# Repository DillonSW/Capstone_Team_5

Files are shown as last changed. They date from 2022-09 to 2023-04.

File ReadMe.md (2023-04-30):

# Class Kit Vending Machine 

## Executive Summary

Every year hundreds of students require various devices for their ECE (Electrical and Computer Engineering) classes. These specific devices are provided by the College of Engineering and are rented out to students through the ECE office. Typically, in the first month of a semester, students attempt to check out on average 50 devices in a day from the Office. This capstone project will focus on designing and implementing a vending machine that can distribute devices out to students while recording which students have checked out a device. The finished product will be a vending machine with the functionality to vend the needed specific devices to students. A student can enter their information into the machine, and the machine will record who has checked out their respective device(s). The machine will use a motor to rotate a device to the door for a student to remove that has LEDs (Light Emitting Diode) which will allow students to see and determine which device is the one they should remove. The student will then take the device and shut the door for the next student.     

## Capabilities

The first prototype of the vending machine has the capability to record all input student data and store to the SQL database held on the host machine. The program can communicate using custom OPC software and read/write tags to turn the motor. The GUI has a loading mode where the admin can enter all devices inside the machine and a delete mode where all data held by the database can be removed. After loading, the machine resets to the initial position to track exactly which board will be rented. The motor is powered through the custom enclosure and is controlled by the PLC. The overall function of the machine allows a student to enter data and quickly receive a response from the machine, returning a board to the student and recording exactly which device was given.  

## Salient Outcomes

The team believes one salient outcome of this project is the development of a base communication program between a host machine and PLC. This project can serve as a platform for future teams to be able to create a full version of the kit vending machine for the ECE department. The communication is specifically between a linux machine and Allen Bradley PLC.  

The team also believes another outcome of the project is the protection of data through research into SQL Injection. This can also serve to teach future teams about data safety when using databases. SQL Injection is an issue many large companies deal with on a daily basis.  

## Project Demonstration & Images

Experimentation Videos:
* GUI system: https://youtu.be/tVvsogPO3sM  
* Safety System: https://youtu.be/iVfy9IWk9oA  
* PLC System: https://youtu.be/Vv9zIDt42ac  

**GUI Image**  

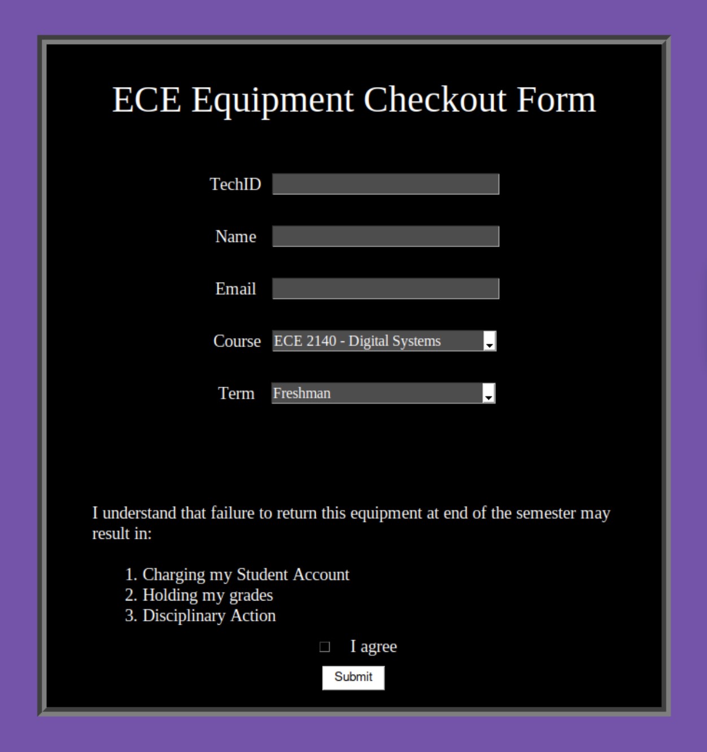
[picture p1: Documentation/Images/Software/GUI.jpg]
GUI
  

**Enclosure Image**  

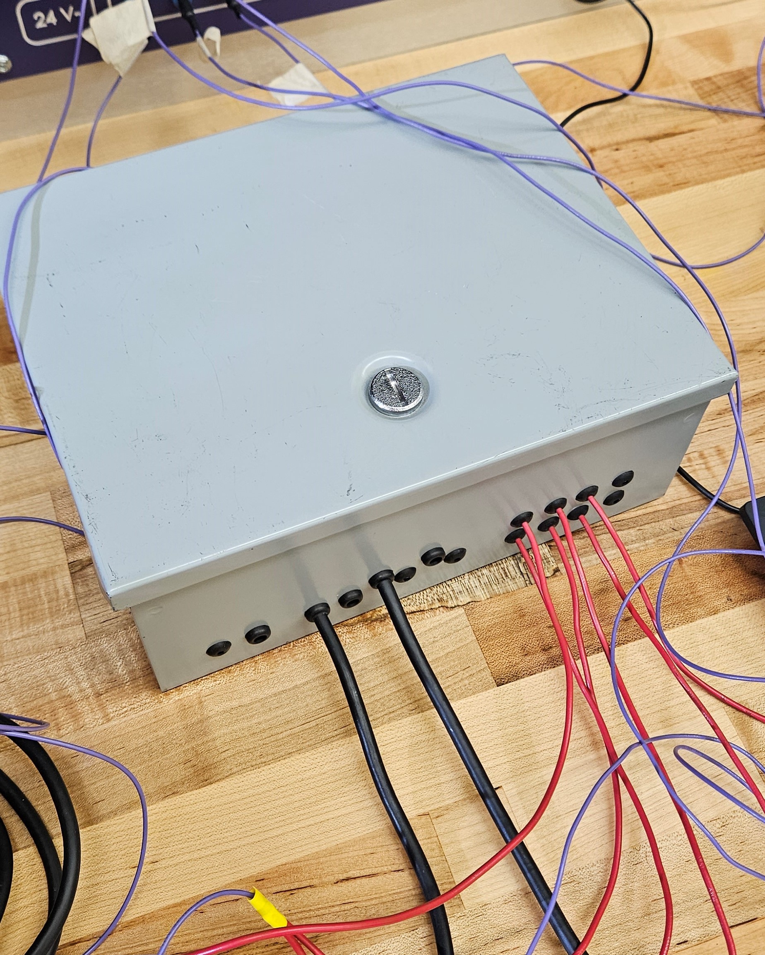
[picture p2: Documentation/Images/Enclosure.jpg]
Enclosure
  

**Safety System and PLC Image**  

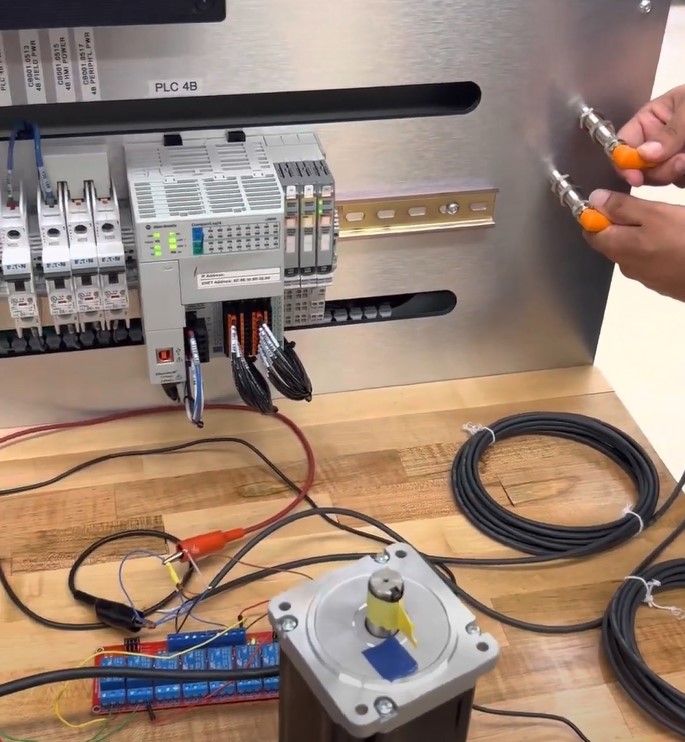
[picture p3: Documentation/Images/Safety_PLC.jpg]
Safety/PLC
  

## Subsystems
* Identification
* Safety
* UI
* Power
* Sensors
* Motor
* PLC
* Security  

## About Us  

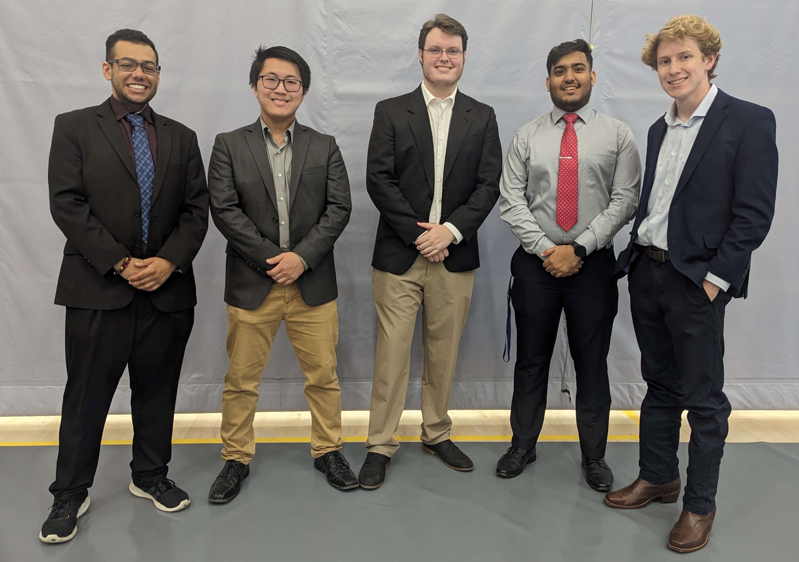
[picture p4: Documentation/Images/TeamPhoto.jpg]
TeamPhoto
  

**Left to Right: Michel Turpeau, Ryan Reed, Dillon Williams, Nidhay Patel, Austin Sigg**  

This team consists of three Electrical Engineers and two Computer Engineers. The three Electrical Engineers are Austin Sigg, Ryan Reed, and Michel Turpeau. The two Computer Engineers are Dillon Williams and Nidhay Patel. The Class Kit Vending Machine is being designed to make the process of renting class devices faster while giving our customers more time for their own responsibilities.  

### Faculty Supervisor

Our faculty supervisor is Dr. Jesse Roberts

### Stakeholders

Our customers are the associates working in the ECE (Electrical and Computer Engineering) office of Brown Hall at Tennessee Tech University.  
The machine should allow more time for associates to complete other responsibilities without being interrupted by students as often.  

### Recognitions

Our Team would like to recognize our partnered Mechanical Engineering Team for their help. The team consists of:  
Carson Pitts, Jessee Millsaps, Mason Baines, and Nathan Bangean.

## Repo Organization

* The Team Contract is present in main  

### Reports

* Conceptual Design and Revisions  
* Project Proposal and Revisions  
* Experimentation
* Lessons Learned

### Documentation

* 3D Models
* Electrical
  * Sources
  * Schematics
* Images
  * 3D Models
  * Schematics
  * Software
* Signoffs

### Software

* Database
* Klaw_rev3
* OPC_rev2
* PLC

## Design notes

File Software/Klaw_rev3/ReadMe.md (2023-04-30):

# Klaw Rev. 3
Klaw came about as a joke the team made during the first semester of capstone.  
We joked we would just make a claw machine where students needed to fish out the device they need for a lab.  

### Function
Klaw3.py is the main functional program of the capstone.  
It contains the code needed to create the GUI, access the database, and message the PLC.

### Dependancy 
* mysql.connector - installed from the same site as the workbench.  
* PySimpleGUI - installed through the command line. Use sudo pip. 
* datetime    - installed through the command line.  
* pycomm3     - installed through the command line.   

### Installation
Install mysql.connector either from the terminal or from the webiste. Make sure it is the connector for python.  
To install all python libraries listed, use: Sudo pip install library_name.  
You can always use: library_name --version to check installations.  
  
### Running
The file can be run through the terminal. You will need to have the OPC operational to actually run the program though.  
The directions for OPC are in the OPC software folder.

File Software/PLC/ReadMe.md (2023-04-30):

# PLC Code

### Function

This software file is the PLC .ACD file for controlling the motor and interacting with the OPC client.

**PLEASE NOTE:** This .ACD file is usable for the Allen Bradley PLCs in the ATC lab in Prescott Hall. If future work is to be done with the gifted Siemens PLC, the .ACD code must be copied over to a ladder logic file in TIA Portal.

The PLC code uses 2 TON timers to control when the motor receives pulses (sort of like PWM). There is a way to be able to do this with 1 TON timer, but I don't remember how. Essentially you must make PLC code for rising-edge detection.

The PLC has 2 tags that are written to by the OPC (Look in the Controller Tags section. Also see the code for the OPC to see the written values). These tags controll whether or not the system is distributing boards, or is having boards loaded.

### Installation

More likely than not, you will be running this code in the PLC labs of Prescott. Download the .ACD file and email it to your Tech email. If you are on a school computer, you could also save it to your lab drive. When in the PLC labs, either download the file from your email or your lab drive. Open Studio 5000 and select Existing Project. From there you should be able to edit the code.

### Running

To run the code, you must select your computer from the dropdown Communication -> Who Active. To do so, you must select Set Project Path. Afterwards, for testing, you must select Communication -> Download. This will save your changes and download them to the PLC. If it does not automatically put you in Run Mode or Online, you must select it again from the Communication dropdown.

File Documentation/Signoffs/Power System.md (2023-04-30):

## Function

This subsystem's function in our design is to tie all of the subsystems together, providing appropriate power to each system. The power coming from the wall outlet will be sent through terminal blocks in our din rail. This 120VAC power will be sent to the PC, and will be converted to 24VDC and sent to the PLC and sensor subsystem.

## Constraints

**The 120VAC wall power:**
* **Will go through a circuit breaker as extra protection for our power system**

^ The 120VAC will feed through a circuit breaker on the din rail, then be sent to the PC, motor driver, and the 120VAC to 24VDC power supply.

* **Will power the PC**

^ A mini PC or "trashcan PC" may have needed a stepped-down voltage. **But because we needed more RAM to run our database and communication servers, a regular PC must be used. These PCs can handle 120VAC input power.**

* **Will be stepped down from 120VAC to 24VDC through the use of a power supply block**

^ This 24VDC will be used to power the PLC and Sensor systems. From there, the PLC will also output 24VDC to control all hardware.

**The 120VAC electrical components:**
* **Will be secured and protected within an enclosure**

^ This closure will be grounded and the components will be secured on a din rail, attached to the subpanel, in the enclosure to ensure the safety of personnel and the machine.

**All of the components**
* **Must be able to fit within an enclosure that can fit within a 35-inch wide space.**

This is the width that we were given by the mechanical team for housing our electrical components.

**The enclosure**
* **Will be grounded and serve in accordance with NEC 250.109**

^ This NEC standard states that "Metal enclosures shall be permitted to be used to connect bonding jumpers or equipment grounding conductors, or both, together to become a part of an effective ground-fault current path. Metal covers and metal fittings attached to these metal enclosures shall be considered as being connected to bonding jumpers or equipment grounding conductors, or both."

^ Source: https://www.electricallicenserenewal.com/Electrical-Continuing-Education-Courses/NEC-Content.php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

This means that we will be able to use our enclosure as an effective ground-fault to protect users, administrators, and maintenance personnel that may be working near the electrical components. We will also have a GFCI power cord for additional safety.

**These constraints will be labeled C1-C6 in the Analysis section**

## Schematic

EnclosurePosition1
EnclosurePosition2
EnclosurePosition3
EnclosurePosition4

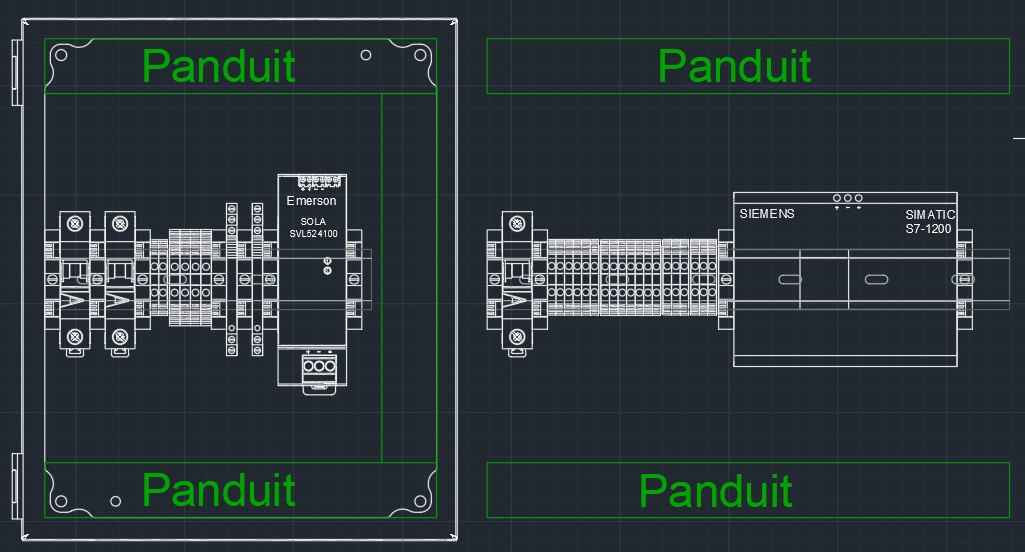
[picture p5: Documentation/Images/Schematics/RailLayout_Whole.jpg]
Dinrail_Layout

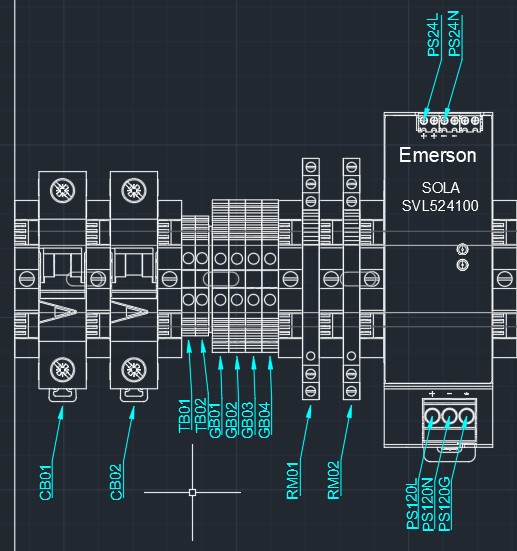
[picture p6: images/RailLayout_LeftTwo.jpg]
RailLayout_Left

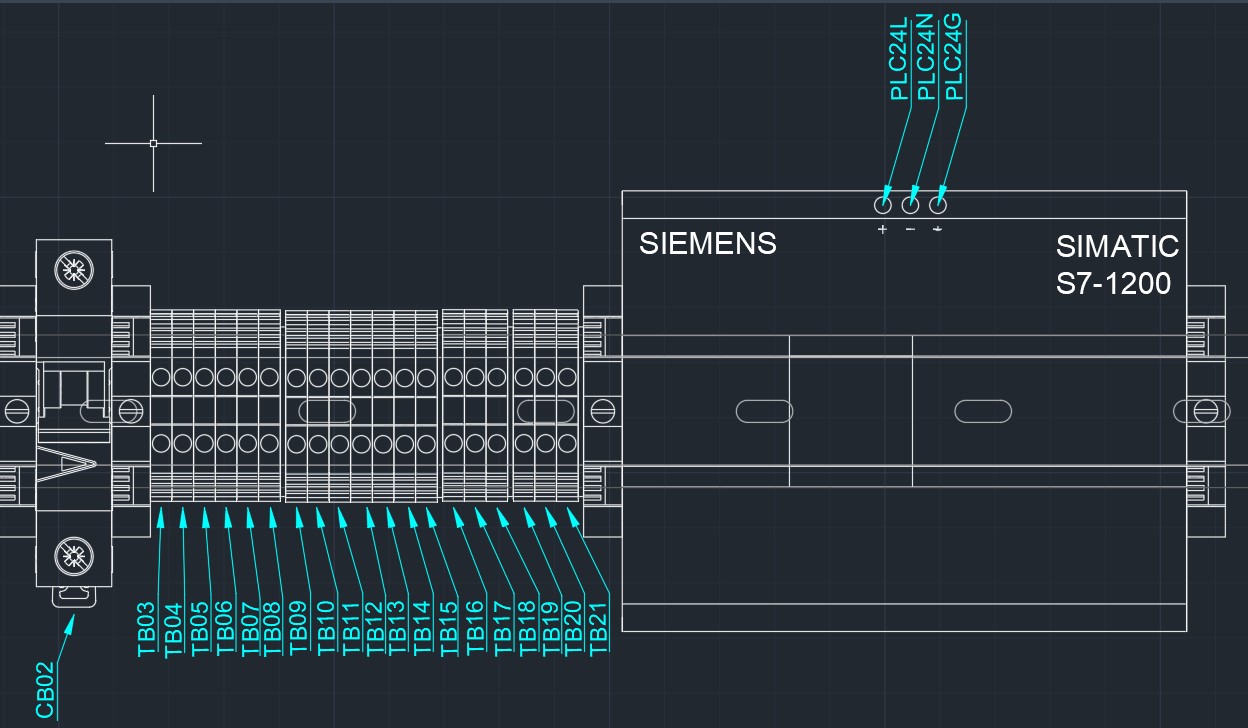
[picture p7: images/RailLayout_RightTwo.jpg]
RailLayout_Right


The AutoCAD schematic above shows the layout of all of our components. All 120V components will be encased within the enclosure and ran through circuit breakers and power cords for safety. The 24V components will be ran outside of the enclosure and through terminal blocks.

**Note: The wires are labeled as the terminal block or component that they are feeding TO, not FROM. Ex. TB02-1 or PLC24L-1.**

Also, the **Motor Driver**, **Sensors**, and **Safety Sensors** have been heavily simplified for convenience of the power system wiring. To see the schematics of the simplified components, please refer to the **Motor System**, **Sensor System**, and **Safety System**.

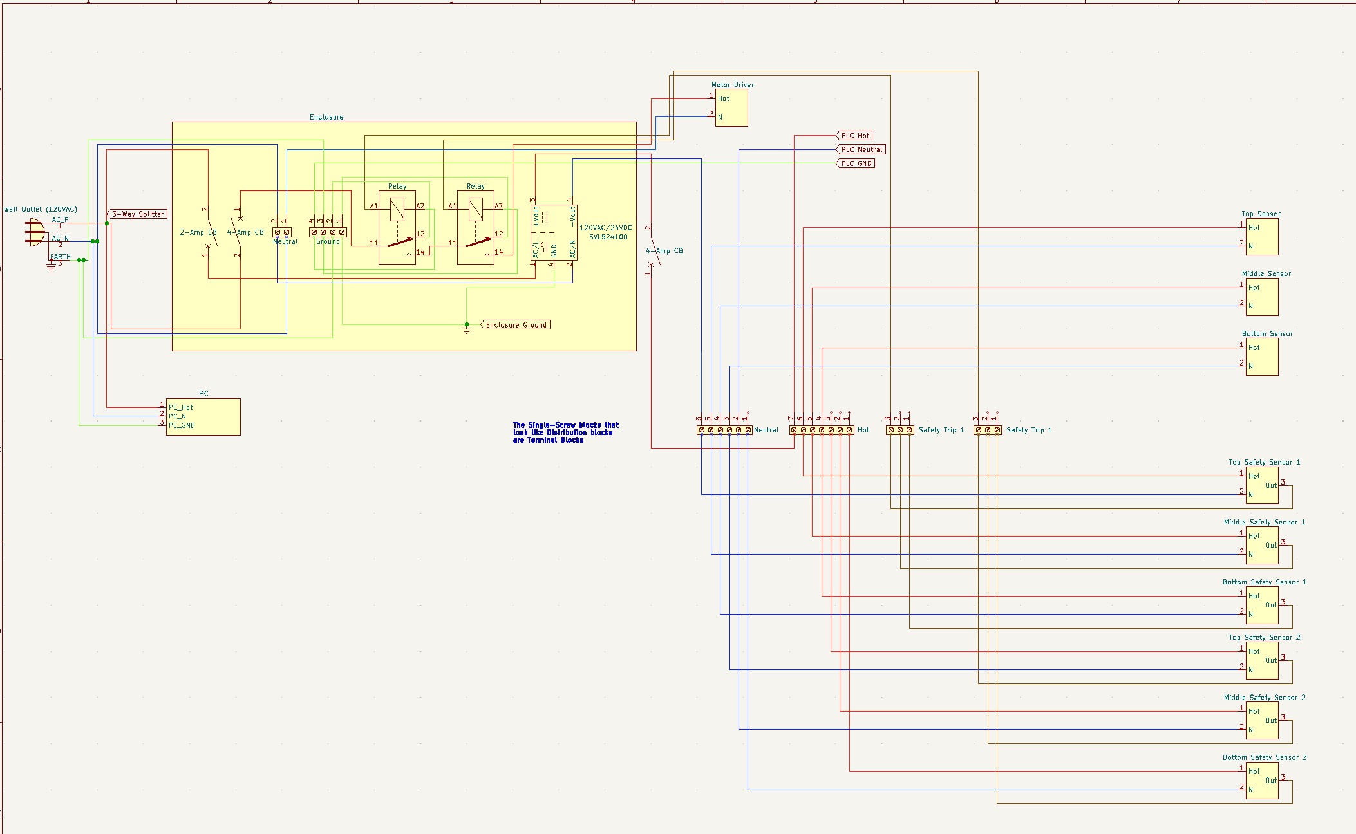
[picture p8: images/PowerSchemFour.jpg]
Schematic


The schematic above shows how the power system will tie every subsystem together. The terminal blocks that are larger than 1x1 indicate that they have been jumped together.

The larger terminal blocks, as stated before, are connected through jumpers. We are buying these jumpers as 10-position connectors. The framework for these jumpers are made of metal. We will cut down the 10-position ones into smaller positions as needed (ex: 2 or 3) with the help of the tools in our machine shops.

## Analysis

## Constraints C3, C4, C6

These constraints are fulfilled through our enclosure and subpanel design. The KiCAD schematics above confirm that we will be using stepping down our 120VAC voltage (**C6**) and that the enclosure will be grounded (**C3**). The AutoCAD and SolidWorks schematics confirm that we will be using an enclosure (**C4**).

## Constraint C5

The din rail and the mounted components must fit within a certain space. We were told by the mechanical team that we will have roughly 35 inches of width to work with. Each component's width will be measured and a subpanel and enclosure will be chosen accordingly.

**Note**
The Hot/Neutral Terminals were rounded up from 0.20 inches to 0.25 inches, a 25% increase for tolerance.

The Ground Terminals were rounded up from 0.24 inches to 0.25 inches.

The End Covers were rounded up from 0.0866 inches to 0.1 inch, which is a roughly 15% increase. This gives the end covers a 15% pre-calculation tolerance.

The Relays were rounded up from 0.244 inches to 0.25 inches.

^ Source: https://www.automation24.com/siemens-cpu-1215c-6es72151ag400xb0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

| Component | Width (inches) | Quantity | Total Width |
|---|---|---|---|
| Hot/Neutral Terminal Blocks | 0.25 | 2 | .5 |
| Ground Terminal Blocks | 0.25 | 4 | 1 |
| End Covers | 0.1 | 1 | 0.1 |
| Stop Blocks (End Anchors) | 0.31 | 7 | 2.17 |
| Circuit Breaker | 0.69 | 2 | 1.38 |
| Power Supply | 1.57 | 1 | 1.57 |
| Relays | 0.25 | 2 | .5 |
|**Total** |  | **Total Width (inches):** | 7.22 |

Without rounding, the actual measurements came out to be 7.055 inches.

We are choosing a subpanel with a width of 9in. This gives us 1.945 inches of clearance. With rounding, we have 1.78 inches.

## Constraints C1 and C2

**Analysis for 120V-side current draw**

To determine the power cord and circuit breaker, we must analyze how much current each 120VAC component will draw. The following is a list of the components and their draws.

* 120VAC to 24VDC Power Supply (120 Side): **1A**
$V1 * I1 = V2 * I2$

$V1 = 120$, $I2(Max) = 5A$, $V * I = 120W$

$120 * I1 = 120$

These equations give that the 120V side will draw, at max, 1A. The 24V side will draw, at max, 5A. **The 24V side will be further analyzed to see how much current it will actually draw**

* PC: **Consumer Rated**

We will be using a power splitter cord to redirect the 120VAC to the PC, located outside our enclosure. Because the PC is consumer-rated, there is not a need to protect it.

* Motor Driver: **2.5A**

The motor driver datasheet states that it will draw 2.5A. Please refer to the Motor System branch to find the datasheet.

We want the motor to be secured by a safety system. We will be using a system of relays to create a redundant system. Please refer to the Safety System documentation to see the schematic.

So, assuming we will only fill to 80% of the current limit, we will need at least a 1.25A circuit breaker for the power supply, and a 3.125A for the motor driver. We are going to use a 2A circuit breaker for the power supply, and a 4A circuit breaker for the motor driver.

We also want the circuit breaker to be higher rated than the power cord. We will use a 5A GFCI power cord.

**Analysis for 24-side current draw**

To determine the fuse breaker protecting the 24VDC components, we must analyze their current draw of all of the components.

* PLC: **1.5A**

The side of the PLC states that it will draw 1.5A.

* Box Sensors: **.025A each**

There are 3 box sensors (top, middle, bottom). Therefore the total current draw will be **.075A**.

* Safety Sensors: **.2A each**

There are also 6 safety sensors (top, middle, bottom; two on each level). Therefore the total current draw will be **1.2A**.

**Total 24V-side current draw**

$1.5 + .075 + 1.2 = 2.775$

Assuming that 2.775A is 80% of max capacity, we must have a fuse breaker that is at least 3.468A. We will use a 4A fuse breaker.

## BOM

| Name of item | Description | Subsystem | Part Number | Manufacturer | Quantity | Price | Total |
|---|---|---|---|---|---|---|---|
| Terminal Blocks | 20A, 600V, Feed Through, Screw, 26-12 AWG | Power | KN-T12GRY-25 | Konnect-It | 1 (Pack of 25) | $8.50 | $8.50 |
| Ground Terminals | 800V, Feed Through, Screw, 26-12 AWG | Power | 1010100000 | Weidmuller | 3 | $4.27 | $12.81 |
| Terminal Covers | End Cover Brackets | Power | KN-ST1GRY | Konnect-It | 1 (Pack of 25) | $11.00 | $11.00 |
| 10-Block Jumpers | Screw-Down, 10 Positions | Power | KN-10J12 | Konnect-It | 1 (Pack of 5) | $10.50A | $10.50 |
| End Anchors | Snap-On, Din Rail End Anchors | Power | 1492-EAJ35 | Allen Bradley | 10 | $2.42 | $24.20 |
| Circuit Breaker | 1-Pole, C Curve, 277VAC/48VDC, 4Amp Circuit Breaker | Power | FAZ-D4-1-SP | Eaton | 2 | $15.00 | $30.00 |
| Circuit Breaker | 1-Pole, D Curve, 277VAC/48VDC, 2Amp Circuit Breaker | Power | FAZ-D2-1-SP | Eaton | 1 | $15.00 | $15.00 |
| 24VDC Power supply | 120VAC to 120W, 24V, Din Rail Power Supply | Power | SVL524100 | Sola-HD | 1 | $70.88 | $70.88 |
| Wire Duct | 1.26in Wide, 1in Depth, Slotted, Lead-Free PVC, Screw Mount Wire Duct | Power | F1X1LG6-A | Panduit | 1 | $29.02 | $29.02 |
| Wire Duct Cover | 1.26in Wide, 1in Depth, PVC, Flush Wire Duct Cover | Power | C1LG6-F | Panduit | 1 | $7.05 | $7.05 |
| Enclosure | 12H x 10W x 6D (in), Wall-Mount, Single Door, Carbon Steel Enclosure | Power | SCE-1210ELJ | Saginaw | 1 | $107.00 | $107.00 |
| Subpanel | 12H x 9W (in), 14 Gauge, Carbon Steel Subpanel | Power | SCE-12P10 | Saginaw | 1 | $11.50 | $11.50 |
| Din Rail | 19.7-inch, Slotted, Steel Din Rail | Power | 467406 | RS PRO | 1 | $4.99 | $4.99 |
| Power Cord | GFCI, 10-ft, In-Line, Vending Machine Cord | Power | 30376018-01 | Tower Manufacturing Corporation | 1 | $77.76 | $77.76 |
| Power Splitter | 2-ft, 14 AWG, 3-Splitter Power Extension | Power | PW163-1324 | Nema | 1 | $6.80 | $6.80 |
| Splitter Cords | 6-ft, 14 AWG Power Cord | Power | PW116-1206 | Nema | 3 | $4.74 | $14.22 |
| Cable Entry Plate | 14 Entry, Screw Mounting Cable Entry | Power | KEL-DPZ 63/14 | Icotek | 1 | $26.11 | $26.11 |
| M12 Cable Gland | M12, Waterproof, Adjustable, Locknut, 3-6mm, Nylon Cable Gland | Power | A16101800ux0286 | uxcell | 2 | $6.49 | $12.98 |
| Fuse Terminal | W-Series Fuse Block | Power | 402363 | Weidmüller | 1 | $6.61 | $6.61 |
| Fuse | Fast-Acting 4A Fuse Breaker | Power | 5ST 4-R | Bel Fuse Inc. | 1 | $9.99 | $9.99 |
| Danger Sign | 120V OSHA Danger Sign, 3.5" x 5" | Power | S-2260 | MySafetySign | 1 | $5.20 | $5.20 |
| **Total** |  |  |  | **Total Components** | 36 | **Total Cost** | $502.12 |

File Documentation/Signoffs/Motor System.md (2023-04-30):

# Motor System

## Subsystem Function

This subsystem's role in our design is to move new devices to the checkout door by receiving power from our power subsystem and rotating the platforms holding the devices. This will only be done when the machine senses that there is a device missing from the checkout drawer. After discussing with the mechanical engineering team, we have decided to make the platforms out of acrylic and the hollow tube inside our machine to be either **aluminum** or **pvc**.  
 
## Constraints

* **The boards being rotated on the platforms (box and all) weigh 0.5lbs**  
^ Each platform will be able to hold 20 boards

**The platforms being rotated by the motor:**  
* **Will be made out of acrylic**  

* **Will be 3.175 mm (1/8 inch) thick, 3 feet in diameter, and have a 16" hollowed diameter in the center.**  
^ This will make the platforms like hollow rings. 

* **Will weigh 3.937 lbs each**  
^ 1/8" acrylic weighs 0.694 lbs/sq. ft. https://www.usplastic.com/knowledgebase/article.aspx?contentkey=884 
Area of circle = 78.540% area of square with same diameter: $(pi*0.5^2)/1 = 0.78540$  
(Weight of whole, 3' diameter, 1/8" thick circle) - (Weight of missing, 16" diameter, hollow center) = 4.906 - 0.969 = **3.937**.  
Material of platform: Acrylic  

* **The platforms will have a flexural strength of at least 4351.13 PSI** 
^ The lowest flexural strength of 64 cast glass specimens was 30 MPA, which equates to 4351.13 PSI. Even though the flexural strength of acrylic is x3 or more that of glass, assuming acrylic's flexural strength is equal to glass can be our worst-case scenario.  
^ Source: https://link.springer.com/article/10.1007/s40940-021-00151-z  
Flexural Strength: 16,500 PSI (6mm thickness)  
^ Source: https://www.builditsolar.com/References/Glazing/physicalpropertiesAcrylic.pdf  

* **Given these calculations, the total weight of the platforms and boards will be 44.811 lbs.**

* **The platforms will also have a 1 in. gap between them and the frame of the machine.**

**The dividers on each platform:**
* **Will also be made of acrylic**  

* **Will be 1/16th inch thick (giving a density of 0.365 lbs/ sq. ft.)**  

* **Will be large enough to encompass the whole board (8.5 x 8 inches, will assume 9 x 9 inches).**  
^ There will be 20 dividers per platform, equating to 60 total platforms.  

* **Given these values, each divider will weigh 0.27375 lbs (0.365 * 0.75). The total weight of the dividers will be 16.425 lbs.**  

**The hollow cylinder supporting the platforms:**  
* **Will be made of aluminum or pvc (assuming aluminum for worst-case)**  

* **Will be 36- to 40-inches tall (assuming 40 inch for worst-case).**  

* **Will be 1/16th or 1/8th thick (assuming 1/8th inch for worst-case).**  
^ Given the density of aluminum (2.7 g/cm^3) and given the area equation for a hollow cylinder  

$M = (π)(h)(mD)(r^2 - (r - t)^2)$  
where:  
  M = mass of the hollow cylinder
  h = height  
  r = outer radius  
  t = thickness  
  mD = Mean Density of cylinder material  
The hollow aluminum cylinder will weigh **9.622 lbs**  

**The Motor:**
* **Given the calculations above, must rotate a total weight of 70.858 lbs. (We will assume roughly 20% tolerance for error, so for calculations we will use 85 lbs)**

**Circuity:** 
* **Will be protected at 125% the nameplate current rating (3.19A).** This comes from the following codes.

The standard NEC 430.52(D) states "Torque motor branch circuits shall be protected at the motor nameplace current rating in accordance with 240.4(B)

^ Source: https://up.codes/s/rating-or-setting-for-individual-motor-circuit

NEC 240.4(B) is the standard for overcurrent devices rated 800 amperes or less, which allows the use of a higher rated overcurrent device as long as the conditions are met. All of these conditions have been cleared.  
 * The conductors being protected are not part of a branch circuit supplying more than one receptacle for cord-and-plug-connected portable loads.  
 * The ampacity of the conductors does not correspond with the standard ampere rating of a fuse or a circuit breaker without overload trip adjustments above its rating (but that shall be permitted to have other trip or rating adjustments).  
 * The next higher standard rating selected does not exceed 800 amperes.  
^ Source: https://up.codes/viewer/illinois/nfpa-70-2020/chapter/2/wiring-and-protection#240.4_(B)  

The standard NEC 705.12(D)(2) Bus or Conductor Ampere Rating states "One hundred twenty-five percent [125%] of the inverter output circuit current shall be used in ampacity calculations for the following: Feeders, Taps, and Busbars."

^ Source: https://up.codes/viewer/delaware/nfpa-70-2014/chapter/7/special-conditions#705.12_(D)_(2)

* **Will follow the NEC 310-16 Table for its wirings**

This table is for "Allowable Ampacities of Insulated Conductors Rated 0 Through 2000 Volts, 60°C Through 90°C (140°F Through 194°F), Not More Than
Three Current-Carrying Conductors in Raceway, Cable, or Earth (Directly Buried), Based on Ambient Temperature of 30°C (86°F)"

## Schematic

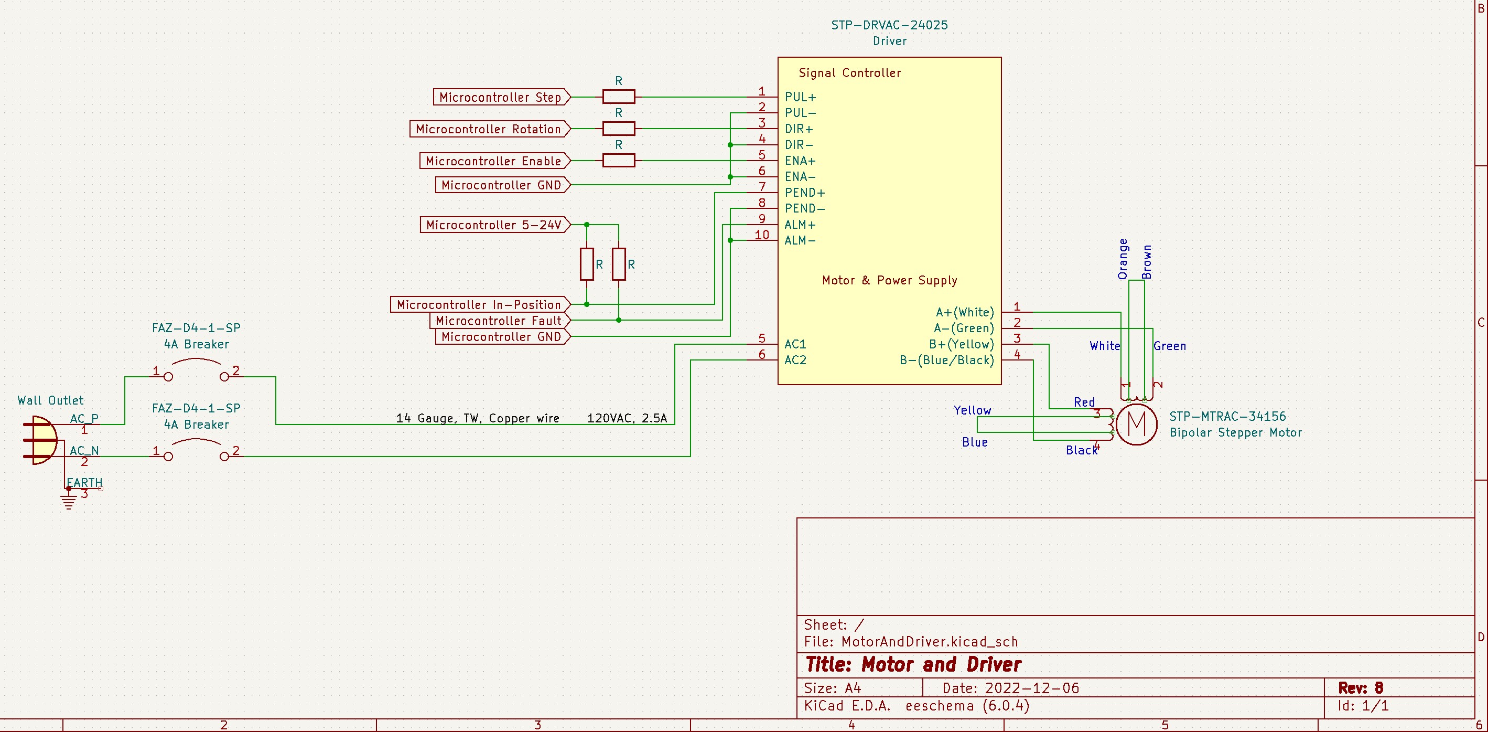
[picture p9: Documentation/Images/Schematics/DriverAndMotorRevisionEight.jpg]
Schematic


The schematic above shows the wiring connections between the microcontroller/microcomputer, driver, and motor. The resistor options for connecting the microcontroller/microcomputer with the driver are: 0 for 5V, 1kΩ for 12V, or 2kΩ for 24V. Because there are 5 resistor connections, 10, 2kΩ resistors would suffice for covering all of them, in which we can use 2, 2kΩ resistors in parallel to create a 1kΩ connection.

This selected dirver and motor will be able to connect and work together. The driver, STP-DRVAC-24025, states "Only use stepper motors wound for high bus voltages (**STP-MTRAC** motors) with high bus voltage drives (STP-DRVAC-xxxxx)." The motor we chose follows this naming convention: **STP-MTRAC**-34156.

Also to note, the STP-DRVAC-20425 driver can take a nominal input voltage of 90-240VAC. Because of this we will not need a step-down transformer.
^ Source: https://www.automationdirect.com/adc/shopping/catalog/motion_control/stepper_systems/stepper_drives/stp-drvac-24025
^ Source: https://www.automationdirect.com/adc/shopping/catalog/motion_control/stepper_systems/single_shaft_stepper_motors/stp-mtrac-34156

The fuses labeled in the schematic are AGC4 fuses. These are "Bussmann fuse, AGC series, small dimension, fast-acting, 4A, 250 VAC, glass tube." This protects the system for 160% of the rated current **and** are the manufacturer recommended fuses.

To adhere to the NEC 310-16 table, the following must be considered:

The datasheet states that the driver will draw 2.5 Amps per phase. Note that this does not mean that it will draw current equal to 2.5 times the number of phases. It simply means that every time the phase is changed, the driver will draw 2.5 Amps.

Because we are getting rid of the transformer, there will be no primary and secondary windings to account for, and there will only be 1 set of wires connecting the wall outlet to the driver. No power analysis is needed because we already know the input voltage and the draw current.

This means the wires must be able to withstand 2.5A.

14 gauge, TW (Or Thermoplastic high-heat resistance and water-resistant) copper wires will suffice for the wires as according to the table, at 140°F, they can withstand a max of 20 Amps. This is well above our expected current draw for the driver.

Based on the table for wire resistances, the DC resistance of 14 gauge, TW, solid copper wiring at 167°F is 3.070Ω per 1000 feet of wiring. We will not use this much wiring.

Assuming we use **at max** 10 feet if wiring, the power losses will be

$L = (I^2)(R)(10/1000)$
$L = (2.5^2)(3.070)(0.01) = 0.1919W$

The losses over the total power of this system will be

$(L/W)(100) = (0.1919/300)(100) = 0.064

This loss is 0.064%. This loss will be minimal, and the transformer will suffice for maintaining the power output we need.

^ Source: https://www.automationdirect.com/adc/shopping/catalog/motion_control/stepper_systems/stepper_drives/stp-drvac-24025
^ Source: https://media.distributordatasolutions.com/ThomasAndBetts/v2/part2/files/File_7437_emAlbumalbumsOcal20(USA)oc_1_g_nec31016pdfClickHerea.pdf
^ Source: https://www.lincenergysystems.com/blog/difference-between-tracer-wire-tw-thw-thhn/
^ Source: http://www.paigewire.com/wire_resistance-prop.aspx?AspxAutoDetectCookieSupport=1

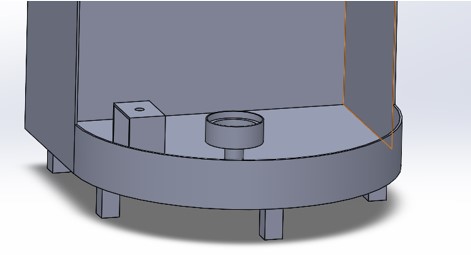
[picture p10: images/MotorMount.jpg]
MotorMount


The image above shows the proposed idea of mounting the motor into the machine. Proposed by the Mechanical Engineering team, the motor will be mounted at the bottom of the machine, and will be on the same level as the mount for the platforms.

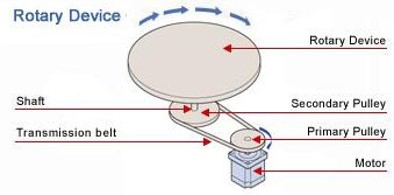
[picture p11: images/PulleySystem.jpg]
Connection


The image above shows the proposed idea of having the motor rotate the platforms. Proposed and discussed by the Mechanical and ECE teams, there will be a gear or belt-feed attatched to the motor's shaft and to the platform's base. These mounts will be of identical size in order to keep the ratio of motor rotation and platform rotation equal. Of course, there will be efficiency loss; any belt-feed or gear ratio will have some sort of loss. As shown in the calculations, we are assuming the worst-case scenario of 50% efficiency.

## Analysis

As stated previously, the motor must be able to output enough torque to rotate roughly 75 lbs. Our current machine design is a hollow cylinder, with the outer diameter being 3' and the inner, hollow diameter being roughly 1'4" 

Below is some algebra that help derive the correct formula to use for our system:

$T = Torque$ | 
$I = Moment of Inertia$ | 
$α = Angular Acceleration$ | 
$a = Acceleration$ | 
$r = Radius$ | 
$m = Mass$

Torque is usually found by multiplying Force and the Radius of the cylinder.

$T = Fr$

Force is equal to mass x acceleration 

$F = ma$

By reorganizing  

$a = F/m$                (1) 

Acceleration can also be expressed as 

$a = (d/dt)(ds/dt)$

For rotatory motion $s = rdθ$

$a = (d/dt)(rdθ/dt)$

Reorganize 

$a = r(d/dt)(dθ/dt)$

Angular Acceleration (α) 

$α = (d/dt)(dθ/dt)$

This means α can be substituted in 

$a = rα$                 (2)

The formula for torque can be reorganized in to 

$F = T/r$                (3)

By substituting equations (2) and (3) into (1), we get 

$rα= (T/r)/m$

Which can be reorganized in to 

$T=mr^2α$

The formula for moment of inertia is 

$I = mr^2$ 

Which can be substituted in as 

$T= Iα$  

Confirming the equation needed to be used to find our Torque.
Since we are working with a cylinder with a hollow center, we are using the equation required to find the moment of inertia for an Annular cylinder

$I= (1/2)M(R1^2+R2^2)$

This equation has been confirmed by multiple sources, and fits into the standards for the equation for moment of inertia

$I = mr^2$ 

$T=W(R1^2+R2^2)/2∗(∆N/308t)$

The equation above is for calculating the torque required to move a certain weight in a hollow cylinder.  

The variables above are defined as:  
T = Required Torque, lb-ft  
WK^2 = Mass Moment of Inertia of load to be accelerated lb-ft^2  
∆N = Change of Speed, rpm  
t = time to accelerate the load, seconds  
W = weight of object, lb  
R1 = outside radius of cylinder, ft  
R2 = inside radius of cylinder, ft  

^ Source: https://www.engineersedge.com/motors/hollow_cylinder_axis_torque_force_equation.htm  
^ Source further explaining equation: https://www.powertransmission.com/ext/resources/issues/0417/baldor-basics.pdf?1646351827

The values of W, R1, & R2 Are consistence since they are the current constraints of our design:  
W = 85 lb 

R1 = 1.5 ft 

R2 = 0.667 ft 

While the values of ∆N & t will vary for testing purposes: 
∆N1 = 5 rpm 

**∆N2 = 3 rpm** 

∆N2 = 1 rpm 

t1 = 0.25 sec 

**t2 = 0.5 sec** 

t2 = 1 sec  

Our current goal is for the rotary device to take roughly 3 seconds to transition from 1 compartment to another. The device would need to rotate 18° to have a complete transition. Luckily for us our choice of stepper motor makes it so each step is 1.8°, which makes it so we have to take exactly 10 steps to reach the next compartment. Using this information, we can determine that are desired rpm will be roughly 1 rpm since 18°/3 sec =6° per second.  

To find the motor that would work best for our project  

Stepper Motors are DC motors that divided a full rotation into a set of equal steps. This will give us greater control on speed and movement of our motor, and the math happens to work in our favor.  

To know what type of stepper motor we need, we have to calculate the torque it will need to properly rotate our device.  

With the known values above, and the values that can be varied, a torque calculation table can be created for each case:  

**Givens:**  
W = 85 lbs  
R1 = 1.5 ft  
R2 = 0.67 ft  

**Required Torque Calculations (lb-ft)**  

|  t(s)  | |∆N (rpm)| |  
|---|---|---|---|
| | 1 | 2 | 3 |
|  0.25  | 1.4872 | 4.4616 | 7.4360 |
|  0.5 | 0.7436 | 2.2308 | 3.7180 |
| 1 | 0.3718 | 1.1154 | 1.8590 |  

**Converted to Nm**  

|  t(s)  | |∆N (rpm)| |  
|---|---|---|---|
| | 1 | 2 | 3 |
|  0.25  | 2.0164 | 6.0491 | 10.0818 |
|  0.5 | 1.0082 | 3.0245 | 5.0409 |
| 1 | 0.5041 | 1.5123 | 2.5205 |  

As shown above, the highest amount of torque required would be at 5 rpm, accelerating in 0.25 seconds. This torque would be 10.0818 Nm.  
However, these results are assuming that a DC motor will be 100% efficient when operating at a lower rated load. This is an unreasonable expectation. Most DC motors are designed to be anywhere from 50-100% efficient with peak efficiency being at around 75% of the rated load. So for a 13 Nm motor, the optimal load range is from 6.5 to 13 Nm, with peak being at 9.25 Nm. Because we would have at most 10.0818 Nm of required torque, and an assumed efficiency of 50% the most torque requited would be 20.1636 Nm. However we are deciding to run the motor assuming a lower acceleration time and rpm. At the values we are expecting to run (0.5s acceleration and 3 rpm), also assuming 50% efficiency, the required torque would be 6.049 Nm, which is close to the acceptable level for our desired motor. 

^ Source: https://www.energy.gov/sites/prod/files/2014/04/f15/10097517.pdf 

A safety measure we must take into account is the potential for a pinch point to occur. According to OSHA 1910.211(d)(44)
* Pinch point means any point other than the point of operation at which it is possible for a part of the body to be caught between the moving parts of a press or auxiliary equipment, or between moving and stationary parts of a press or auxiliary equipment or between the material and moving part or parts of the press or auxiliary equipment. 

^ Source: https://www.osha.gov/laws-regs/regulations/standardnumber/1910/1910.211 

Due to this definition, a pinch point can occur between the dividers and the frame of the machine during platform rotation. This is why we are leaving a 1 in. gap between the platforms and the frame. 

We will assume that the radius from the frame to the pulley / gear is 1.2 ft (or 0.36924 m). 

Given the average width of an index finger is 0.75 in.: 

$T = Fr$

$6.049 = F(0.36924)$ -> $F = 16.3823 N = 3.68289 lb$

We are going to assume that the force acting on a finger in the pinch point will act like shear-force.

The equation for shear-force is: 

$τ = F/A$ 

Where 
$τ = Shear Force$ |  
$F = Force Applied$ | 
$A = Cross-sectional Area, parallel to F$

^ Source: https://www.engineersedge.com/material_science/shear-stress.htm 

For a 1 in. long gap, with an average .75 in. width finger, 

$A = (length)(width) = 0.75 in^2$

So 

$τ = 3.68289/0.75 = 4.91052 lb/in^2$

The max applied shear force on a finger in the given scenario is roughly 5 lb/in^2. This is also assuming that the finger cannot bend. The force required to fracture a "small bone" can be as little as 25 lbs of pressure. It is safe to assume that 1/5th of the minimum force required to fracture a small bone will not cause severe damage. This can be tested by using an object similar to a finger (such as a baby carrot) and rotating the platforms while the carrot is in the door. 
^ Source: https://scienceline.ucsb.edu/getkey.php?key=3088 

If all else fails, there can be a delay for the platform rotating. During this delay, the user interface can display a message to remove any appendages from the machine, or it can be pinched. There can also be a sign attached to the machine. 

**Note**
The torque required to stop the device is well below the holding torque of the selected motor. Also, since this motor has an electromagnetic brake, it will have even greater stopping power assuring the motor does not lose its step. A table displaying the pull out torque is placed below. Pull Out Torque is the maximum torque the brake can output at higher speeds. The higher the rmp, the less it can brake. Our maximum speed (5 rpm) will not come close to being an issue.  
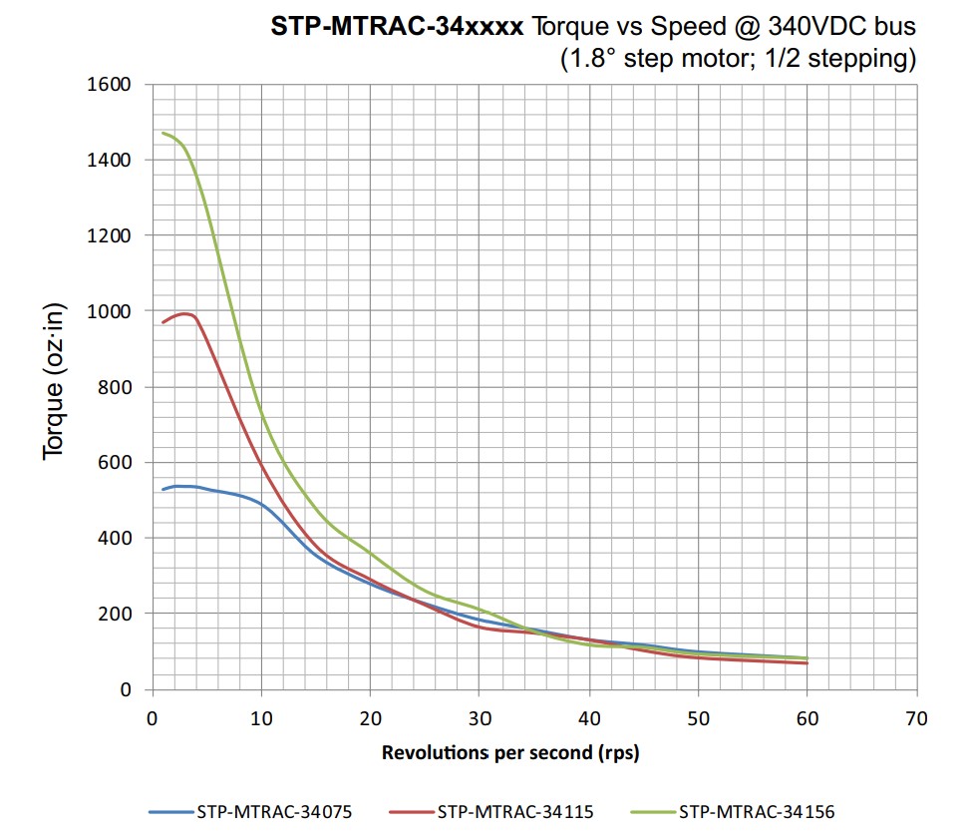
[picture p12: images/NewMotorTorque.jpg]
PulloutTorque


Since the motor we are looking at can have a holding torque of 9 Nm at 5 rps, a higher speed than we intend to run the motor, it will meet the constraints of outputting enough torque and securing the devices. We would be able to operate the motor at a lower demand than its maximum, putting less strain on the motor over time.  

The motor, as stated before, can rotate 1.8° per step. The datasheet does not directly state tolerances for the step angle. However, compared to our previous motor selection, this motor is considerably more expensive. It can be assumed that the precision may be equal, meaning that there is a 0.09 tolerance, meaning the motor can step anywhere from 17.1° to 18.9° in 10 steps. Because the Mechanical Engineering team plans on keeping the rotation ratio between the motor and the platform the same, there will be, at maximum, 0.9° of error per board. This error is allowable, as this is not enough error for the sensor to miss the board during a rotation.

The datasheet gives different amounts of micro steps that the encoder can have. These values can range from 200 to 25600. An encoder's resolution can be represented as pulses per revolution (PPR). Given that the stepper motor we chose has can rotate 1.8° per step, the minimum PPR we would need is

$N = 360/I$

Where

N = Number of points per revolution (or per 360°)

I = Smallest required increment of measurement. For this motor, $I = 1.8°$

Therefore

$N = 360/1.8 = 200$

This means that the bare minimum amount of PPR, or encoder resolution, that we would need to accurately reach our destination is 200. Because the stepper motor driver encoder's resolution can go from 200 to 25600, and resolution will suffice for precisely meeting our specifications. To account for potential error and to further increase the precision and accuracy of our stepper motor, we will choose an encoder resolution of 12800 PPR.

## BOM

| Name of item | Description | Subsystem | Part Number | Manufacturer | Quantity | Price | Total |
|---|---|---|---|---|---|---|---|
| STP-MTRAC-34156 | Stepper Motor for Rotating Platforms | Motor | STP-MTRAC-34156 | SureStep | 1 | $284.00 | $284.00 |
| STP-DRVAC-24025 | AC Microstepping Stepper Driver | Motor | STP-DRVAC-24025 | SureStep | 1 | $213.00 | $213.00 |
| JOS 2 kΩ Resistor | 5% Tolerance, Carbon film, 1/4 Watt | Motor | 10EP5142K00  | E_Projects | 10 | $0.573 | $5.73 |
| FAZ-D4-1-SP | Single Pole, 4 Amp, DIN Rail Mount Breaker | Motor | FAZ-D4-1-SP | Eaton | 2 | $15.00 | $30.00 |
| **Total** |  |  |  | **Total Components** | 14 | **Total Cost** | $532.73 |

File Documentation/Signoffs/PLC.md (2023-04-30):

## Subsystem Function 

The subsystem's role in our design is to control all electronic hardware (locks, LEDs, etc) as well as the motor rotating the platforms. It will also have a communication stream with the microcomputer to inform it when a board is checked out or restocked. 

## Constraints 

**The PLC:** 

* **Must have at least 6 Digital Input pins**

^ These are for the 3 door locks and sensors in order to be read by the PLC.

* **Must have at least 9 Digital Output pins**

^ These are also for the 3 door lock and sensors in order to be commanded by the PLC, in addition to the motor driver's Pulse (PUL) and Direction (DIR) ports.

^ Because all of the locks, sensors, and motor driver ports take 24VDC, the Digital Output (DO) ports will suffice for PLC commanding.

From this, the input module must have at least 6 ports, and the output module must have at least 9 ports 

* **Must be able to fit in a 3x1x1 foot area**

^ This is for clearance in the area where we are going to house all of our controllers and electronics, aside the motor. 

* **Will be in accordance with IEC-61131-2(6.4.4.3) which states:**

"When the short circuit (for a voltage output) or the open circuit (for a current output) is realized, no physical damage or abnormal phenomenon shall be detected." 

This will be accomplished by having a fuse breaker between the 24VDC supply and components.

^ Source: http://rpa.energy.mn/wp-content/uploads/2017/03/IEC-61131-2-Programmable-controllers-Equipment-Requirements-and-Tests.pdf 

* **Must be able to communicate with our PC and database**

^ This is discussed elsewhere; please refer to the Identification System

**These constraints will be numbered C1-C5 during Analysis**

## Schematic 

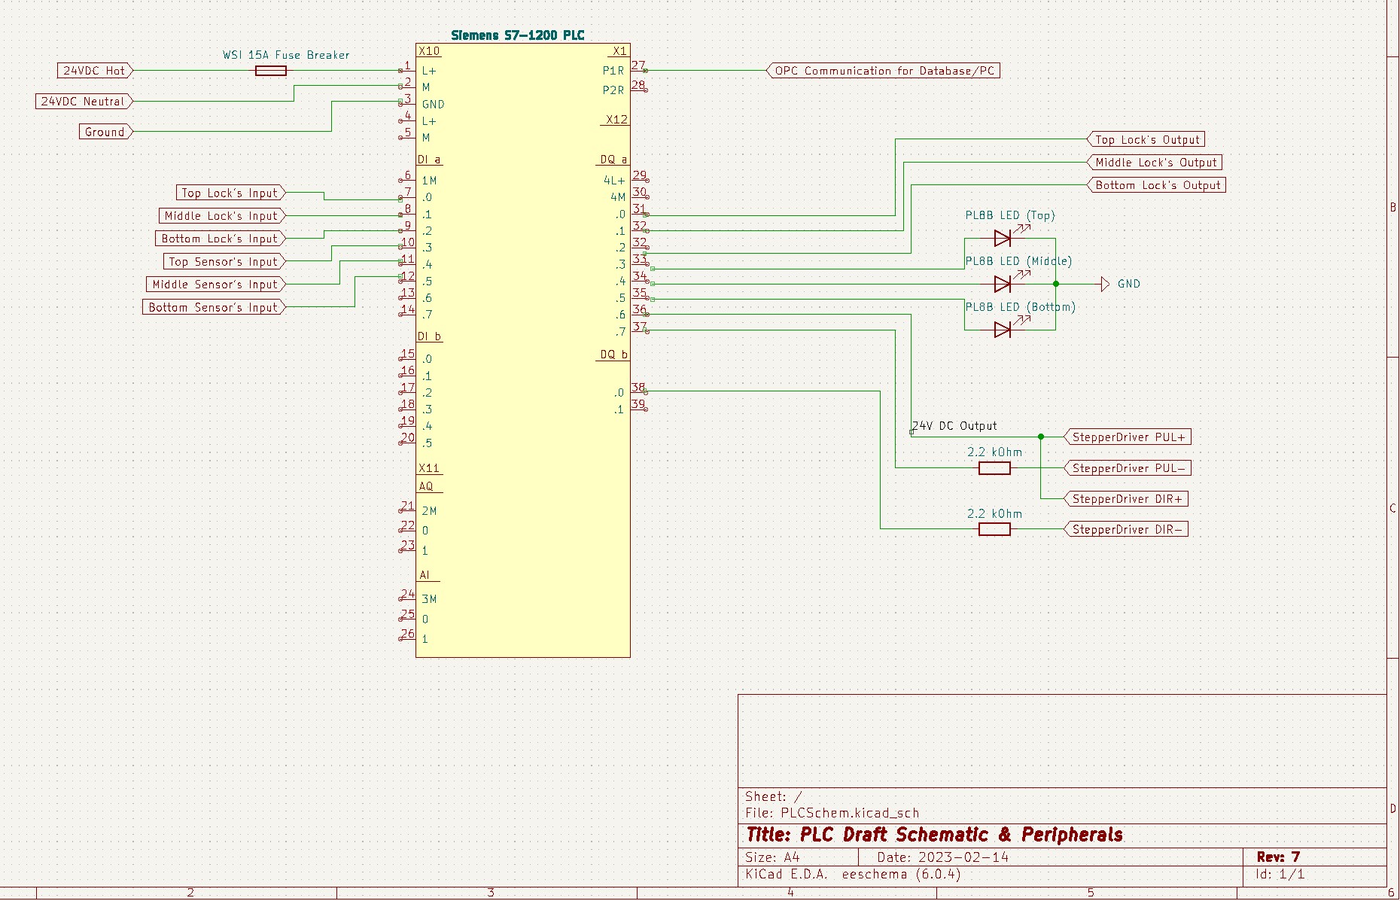
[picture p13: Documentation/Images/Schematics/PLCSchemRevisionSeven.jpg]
Schematic
 
 
Above is a schematic of how the PLC is going to be implemented into our machine. The LED's in the schematic are rated to receive 24V AC/DC. Because of this there is no need for resistors to limit current to the LEDs. The 24VDC side is protected with a 15A fuse, and will be further discussed in Analysiss

The pins on the PLC are also tagged to their respective peripheral. DI a/b are Digital Input ports and DQ a/b are Digital Output ports.

**Discussion about the 120VAC side of the transformer will be in the Power System signoff. Please refer to it**

## Analysis 

**Constraints C1-C2**

^ The datasheet for the PLC states that it has "[Digital] 14 inputs/10 outputs"

^ Source: https://cache.industry.siemens.com/dl/files/465/36932465/att_106119/v1/s71200_system_manual_en-US_en-US.pdf

**Constraint C4**

^ This constraint is discussed elsewhere. Please refer to the Identification Subsystem.

**Constraint C3**

^ This constraint was given to us by the mechanical team as the approximated space that we would have for the electircal components in the back of the vending machine. The following images will show the area that the PLC takes up. The order is length, width, height. The dimensions will also be given below each image in inches and millimeters.

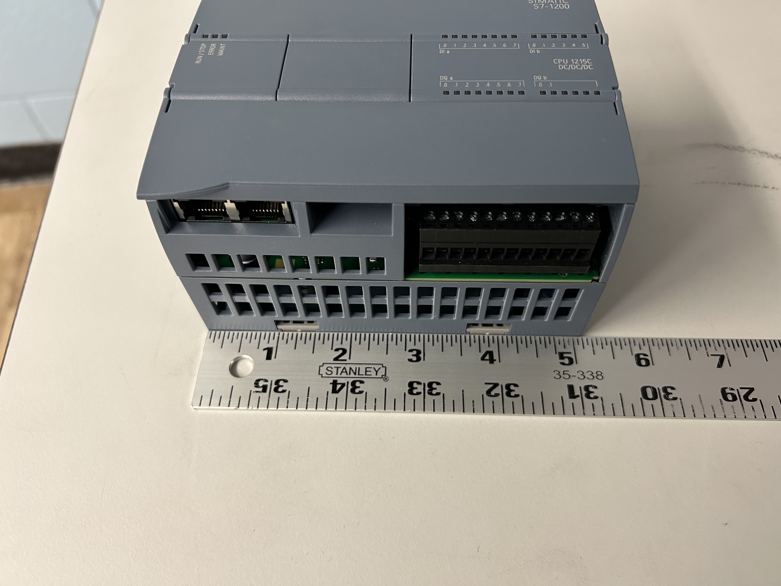
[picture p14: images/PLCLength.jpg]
PLCLength


PLC Length: 5.125 inches (130.175 mm)

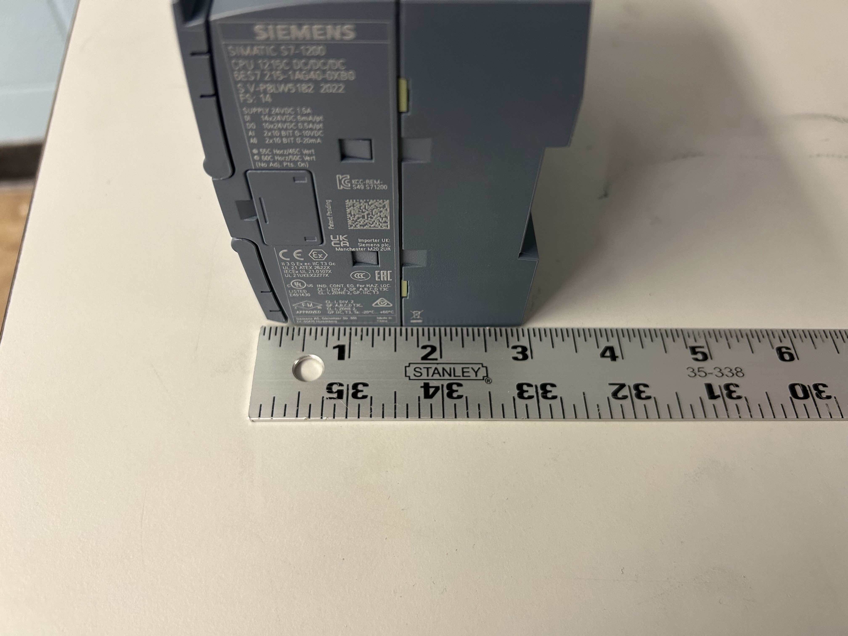
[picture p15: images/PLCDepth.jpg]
PLCDepth


PLC Depth: 3 inches (76.2 mm)

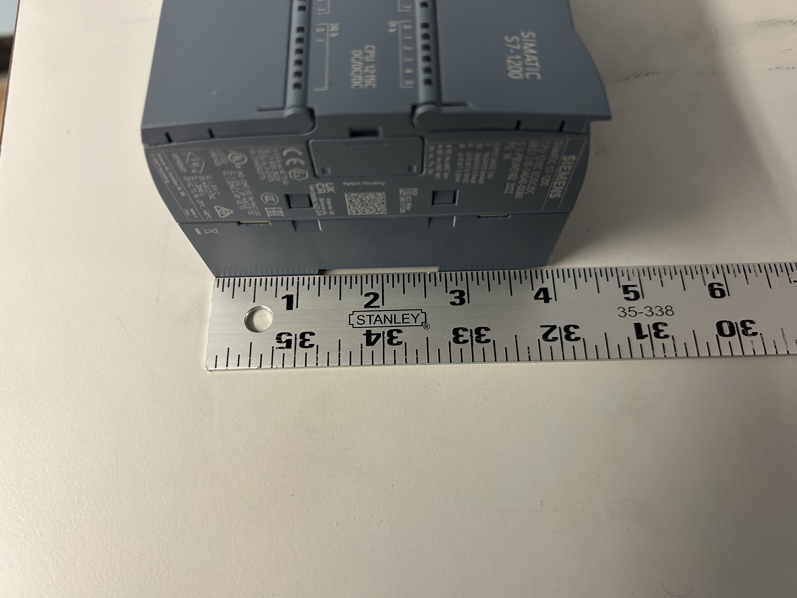
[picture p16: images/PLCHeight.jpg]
PLCHeight


PLC Height: 4 inches (101.6 mm)

Given that our constraint is 3x1x1 feet, our PLC does meet this constraint.

* Constraint: **Will be in accordance with IEC-61131-2(6.4.4.3)**

To protect the 120VAC side of the system, we are using a GFCI cord and circuit breaker on the din rail (This is further discussed in the Power System signoff). To protect the 24VDC side, we must calculate the amount of current that will be drawn from each component. These values are already taking into account the x1.25 storage so that the current draw will not exceed 80% of the maximum. (Again, please refer to the Power System Signoff).

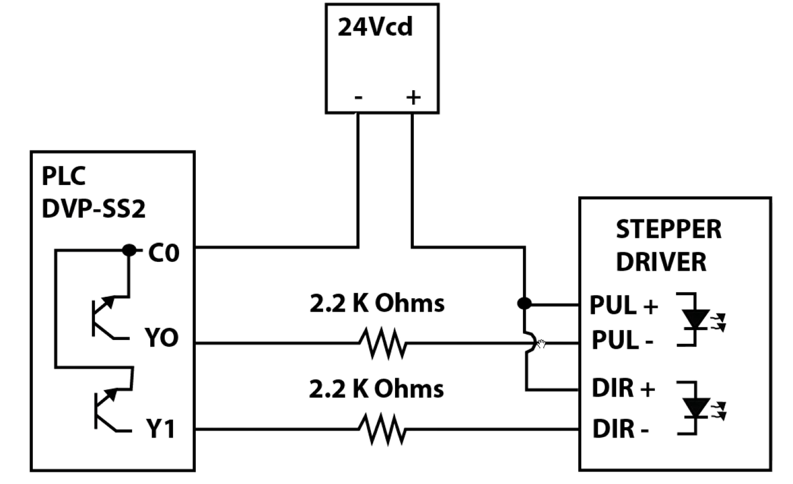
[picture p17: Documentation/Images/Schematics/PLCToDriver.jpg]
PLCToDriver
 

The image above shows how the PLC is going to connect to the motor's driver. The driver's ports will receive 24VDC, hence why the PLC needed 24VDC output pins. The PLC will control the pulses (PUL +/-) and the direction (DIR +/-) of the driver, which will dictate how many pulses the motor will receive and what direction the motor will rotate.

^ Source: https://youtu.be/8hoBHmvRutA (This video is from an automation channel and shows, in great detail, how to connect a PLC to a stpper motor driver)

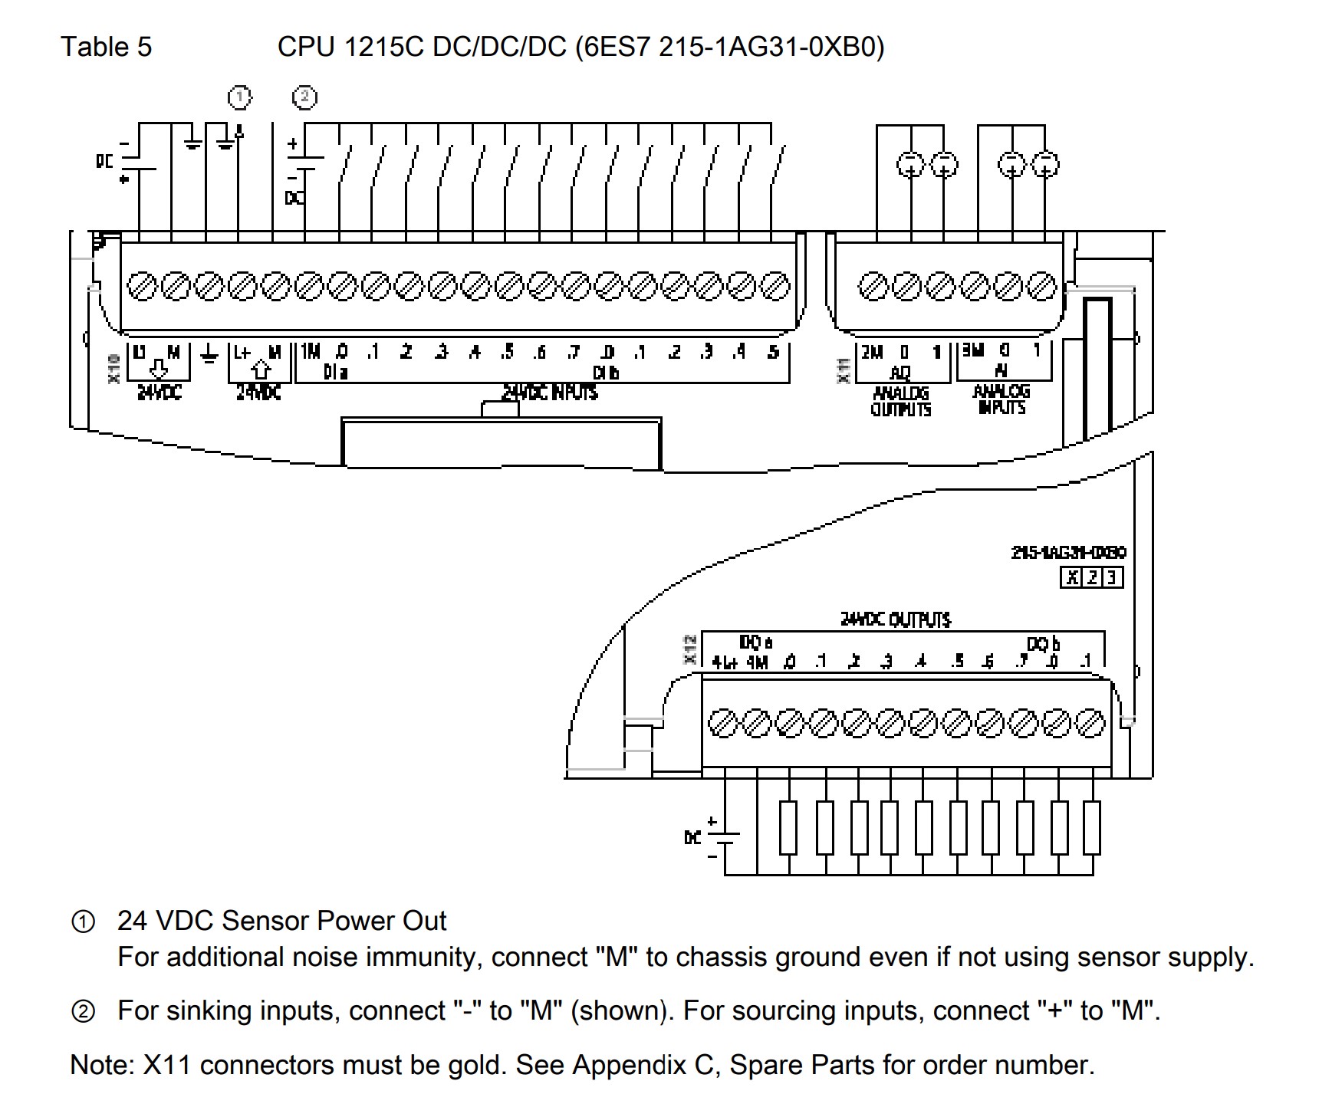
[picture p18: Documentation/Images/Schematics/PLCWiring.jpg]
Wiring


The image above shows how the PLC is wired internally to its inputs and outputs, and how it will be powered. The diagram shows that from a 24VDC power supply, the V- terminal will be connected to "M". The reason there are two wires is because the V- can act as the "ground" of the power supply, however it is still treated as V- and not common ground for the system. The V+ side will only be connected to "L".

^ Source: file:///C:/Users/ryanr/Downloads/technicalinfodoc_2702079%20(6).pdf

## BOM 

| Name of item | Description | Subsystem | Part Number | Manufacturer | Quantity | Price | Total |
|---|---|---|---|---|---|---|---|
| PL8B LED | 24V AC/DC LED | PLC | PL8B-24 | AlpineTech | 3 | $5.95 | $17.85 |
| Siemens S7-1200 PLC CPU | 14 Digital Input, 10 Digital Output | PLC | 6ES7214-1BE30-0XB0 | Siemens | 1 | $464.03 | $464.03 |
| **Total** |  |  |  | **Total Components** | 4 | **Total Cost** | $481.88 |

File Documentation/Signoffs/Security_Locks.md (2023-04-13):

# Security & Locks

# Subsystem Function:
This subsystem's role in our design is to secure both the stored devices and internal components of the machine. The main contributor to the security system will be the cabinet doors holding the devices. These cabinet door require digitally controlled locks, allowing access to verified users, while locking out those who would attempt to forcefully steal from the machine.

# Constraints

**• The locks shall respond to the commands of the PLC. (CL-1)**
	
**• The locks shall remain extended when power is lost. (CL-2)**

	• To prevent possible theft of inventory, the locks shall stay locked in all instances of power loss. 
	• The locks shall only be unlocked if instructed by the internal operations of the device.

**• The inductance sensors shall inform controlling PLC of lock status at all times. (CP-1)**

**• There shall be visual indicators to inform the user of the location of their device. (CI-1)**

**• The door shall open as soon as locks are released, preventing the door re-locking before device is removed. (CS-1)**

**• The locks shall resist the force of resisting spring force of internal spring hinges. (CS-2)**

	• The main purpose of the machine is to /contain and distribute valuable technology. 
	• Knowing that there might be attempts to break in, the locks must be strong enough to resist the average human's strength.
	
**• Unauthorized users of the device shall not be able to access internal contents. (CD-1)**

## Full Schematic



## System 3D Model





Shown above is the current design of one of the cabinet doors. The front of the machine will have 3 cabinet doors, one on each level of the rotating platforms. They act as the sole consumer accesspoint and protect the contents of the cabinet. Each door comes with a solenoid lock, inductance sensor, and an adjustable hinge.

When a costumer completes the rental process, the solenoid lock will release and the spring-loaded hinge will push the door open. This allows the user to take the contents of the cabinet, their newly registered device. The user would then push the door close, returning the door back to it's original state. This confirmed by inductance sensors placed at the strike plate of every lock. (Note: The machine can **NOT** continue any operation until the door is closed. For more see the [Safety System](https://github.com/DillonSW/Capstone_Team_5/blob/Team5-signoff-Safety-System/Documentation/Signoffs/Safety_System.md).)

# Analysis

## Locks



^Source: https://www.uxcell.com/12v-11a-114mm-electromagnetic-solenoid-lock-assembly-for-electirc-door-lock-p-1634595.html

Solenoid Locks use a small electromagnet to control the plunger of the lock. When the solenoid is unpowered, the lock's plunger rest in its extended "locked" state. However, when the solenoid is powered the lock's plunger is pulled back allowing the cabinet door to be opened. This allows us to digitally control the locking state of the cabinet doors. This process is controlled by the PLC. 



^Source: https://electronics.stackexchange.com/questions/86443/need-a-loud-electrical-component-for-magnetic-lock

The solenoid locks will be attached to the enclosed side of the cabinet doors. There will also be protection provided to the body and wires of the locks to help prevent tampering and/or vandalism. The material of the protective shell will be determined by the mechanical team.

For the solenoid locks to be activated, they will require a voltage of 9V-12V and current 1.1 A. These charges will be controlled by the PLC, which they are directly wired to. (CL-1)

In the case power loss and/or blackout there is little to no loss in security, since the locks only release when the solenoid is powered. (CL-2)

### Solenoid Schematic


The Schematic above shows that the **Red Wire** will be connected directly to the PLC, and the **Black Wire** to ground.

## Proximity Sensors
As both a safety precaution and security measure, there needs to be a confirmation of the door being closed and the lock being locked.



^Source: https://files.pepperl-fuchs.com/selector_files/navi/productInfo/pds/085298_eng.pdf

To confirm the state of the locking mechanism, there will be an inductive proximity sensor installed on each level. An inductive proximity sensor only detects the presence of metallic objects, making it difficult for tampering. This proximity version of the sensor has a detection range of 4mm, allowing room for error for contact. This also prevents damage being done to the sensors every time the plunger enters the strike plate.

The proximity sensors they will also be directly connected to the PLC. Their connection will remain open as long as they are in proximity of the lock plunger. They will close their connection with the PLC every time the plunger of the lock is missing from the strike plate. (CP-1)

The proximity sensors will be installed into the sides of the opening of the cabinet doors. They will be directly aligned with the solenoid locks.

### Sensor Schematic



## LEDs

As a visual aid, there will LEDs next to the door present at each level. When the consumer is complete rental process, the door will pop open and the LED next to it will start blinking. While this is not a necessary function, it is a useful feature to assist the consumer. (CI-1)



^Source: https://www.amazon.com/Alpinetech-Metal-Signal-Indicator-Pilot/dp/B06XXPZBKQ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

After the door has been confirmed to be closed, the LED will turn off and return to standby mode.

### LEDs Schematic


## Spring Hinges
To assist the user with identifying their cabinet door, there will be spring hinges installed. This will also help with the locks being moved away from their strike plates, keeping the door unlocked if the user was too slow to open the cabinet door. (CS-1)

These hinges will constantly be applying force outward to push the door open, and should be easy to close back into the locked state. While there will be slight presser on the solenoid locks, there will not be enough to do damage to them. To assure this, adjustable spring locks will be used. This will allow the alteration of spring's tension. (CS-2)



^Source: https://www.hingeoutlet.com/products/spring-loaded-hinge-for-cabinets-304-stainless-steel-sold-individually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

As shown in the diagram above, the hinges will constantly be in the "Opening Tension Type (SO)". Constanly trying to push outwards to open the door.

## Door's Design

The current design of the doors are shown below.



Each door shall have mounting for a solenoid lock and a SensaGuard actuator (See [Safety System](https://github.com/DillonSW/Capstone_Team_5/blob/Team5-signoff-Safety-System/Documentation/Signoffs/Safety_System.md))

Since there will be spring hinges installed on each door, the risk of handles can be eliminated. This will prevent possible vandalist from using brute force to pry open the cabinet doors. (CD-1)

# BOM
| Name of item | Description | Subsystem | Part Number | Manufacturer | Quantity | Price | Total |
|---|---|---|---|---|---|---|---|
|11.4mm Electromagnetic Solenoid Lock| DC 12V, 1.1A | Locks | a19042500ux0016 | uxcell | 3 | $12.49 | $37.47 |
|Proximity Inductive Sensor| PNP Normally Open Two-wire| Safety |NBN4-12GM60-WS-V12 | PEPPERL & FUCHS | 3 | Provided by school | N/A |
|3.5'' Self-Closing Door Hinges| Stainless Steel Adjustable 3 Pack |Locks|B08YZ2TF1F|Qkenvo| 1 | $27.99 | $27.99 |
|Signal Indicator Pilot Dash Light| 8mm 5/16" 24V AC/DC LED |Locks| PL8B-24 |Alpinetech | 3 | $5.95 | $17.85 |
| **Total** | | | | **Total Components** | 10 | **Total Cost** | $83.31 |

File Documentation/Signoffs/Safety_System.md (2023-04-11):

# Safety System

## Subsystem Function:
The sole purpose of this system is to secure the safety of both the users and the operators of the device. The primary functions of the system come from the consumer's cabinet restrictions. Using "SensaGuard" non-contact Interlock technology, both the consumers and inner contents of the machine shall have an extra shield from possible harm. This shall also protect the integrity of the vending device's processes, it can be considered a type of oversheilding for the device's functions.

## Constraints:

**• The relay shall be aware of the state of each cabinet door at all times. (C1)**

**• The system shall be redundant and separate from the normal operations of the PLC. (C2)**

**• The system must overrule all other functions of the system. The motor shall not have any motion while there is an error in place. (C3)**

## Subsystem 3D model



## Subsystem Schematic



  **Note: For alternative design with no non-contact interlock switches, please refer to the schematic found [here](https://github.com/DillonSW/Capstone_Team_5/blob/4dd55fb676e405559dcd8b679fd0daf48392436e/images/SafetySystem_Schematic_ACTUAL.png).**

## System Design:

  At the frame of each door there will be a safety sensor and its paired actuator. These sensors are then wired in series and connected to the Dual-Check Relay System to be monitored. Also, the relay will control when the motor will be given power since it is directly connected to the motor's power supply. **(C1)**
  
  This system will work in parallel to the main system's functions, and operate separately from the main operations of the machine. The system is designed to be redundant to ensure the safety of the users. 

# Analysis:

### Dual-Check Relay System



  The Dual-Check Relay System is comprised of two terminal block relays connecting the power of the motor in series. The relays will be connected to the outputs of the non-contact interlock switches, and will report when any switch is missing the signal of their actuator. Relay_1 will be connected to the OSSD 1 Output, and Relay_2 will read in the OSSD 2 output. If either of the sensor signals are lost, the power of the motor is disconnected and will be unable to function.

### Non-contact interlock switches

After doing some research, it was found that using Non-contact interlock switches would work best for the vending device. Using RFID technology, these sensors have several layers of protection and are considered to be the **"Gold Standard"** for RFID coded safety sensors.

    Note: The "Gold Standard" phase is sourced from Professor Jesse Roberts of Tennessee Technological University



^Source: https://us.idec.com/medias/safety04-03-eng.jpg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

> A non-contact interlock switch is a device that uses a sensor head to detect the distance between an actuator mounted to the door and a sensor head mounted to the machine and to detect information from the actuator without any direct contact between the actuator and the sensor head, and transmits the signal as door open/close information.

^Source: https://us.idec.com/idec-us/en/USD/RD/safety/guide/safety04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,and%20transmits%20the%20signal%20as%20door%20open%2Fclose%20information.

    Note: Since the sensors are "non-contact" they will not gain much wear and tear. 
    However, it is recommended to inspect the sensor every month for any oddities. 
    
These sensors will "report" the state of the cabinet door by have constant connection to their actuators. Whenever the sensor loses this reading, the signal connected to the relay will disappear and the relay will release the connection to the motor's power supply. **(C3)**

### Anti-tampering Function

There are two types of RFID type anti-tampering functions: Unicode type and Multi-code type. The SensaGuard uses the Unicode method. This means that there is single specific code matched between the sensor and actuator. There is also a feature for pairing the new actuator to the sensor after purchase.



^Source: https://us.idec.com/medias/safety04-07-en.jpg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

And as stated in the System Design, the state of the safety sensors will work in parallel with the induction sensors. The induction sensors are a part of the normal system functions, while the safety sensors act as a monitor of the door. The induction sensors can be tampered with nearly any piece of metal, meaning the safety sensor's coded RFID is the real line of defense. **(C2)**

### Adaptation



*^Table 2*

As seen in the diagram above, the output cable has a total of 8-pins. Each of these pins need to be connected to separate parts of our system to be properly utilized. Also, to simplify the process the sensors will be connected in series. By doing this if any of the sensors are missing their actuator or are out of line, the system will report 0V to the Safety Relay. Using Kicad a wiring model was constructed based on the sample model provided by the manufacturer. Sample seen below:



*^Figure 5*

## Placement and Alignment 

Each sensor will be placed on the inner side of the door frame, below the induction sensors (See [Locks System](https://github.com/DillonSW/Capstone_Team_5/blob/main/Documentation/Signoffs/Security_Locks.md)). The component's dimensions are reflected in the 3D mock up below. (Values in inches)





The sensor component and actuator require a minimum distance of 1.97" of space betwixt them. This is shown in *Figure 3* from the user manual on the manufacturer's website.



*^Figure 3*

These conditions are reflected in the mock up 3D model shown below. (Full model at top of page)



    Note: It should also be noted that only the sensor piece of the pair requires a wired connection. 
    This means the actuator doesn't require any extra components or wiring attached to the door.
**Table 2, Figure 5, and Figure 3 are from the *SensaGuard Rectangular Flat Pack Installation Instructions* found [here](https://www.rockwellautomation.com/en-us/products/hardware/allen-bradley/safety-products/safety-sensors/safety-interlock-switches/non-contact-interlock-switches/440n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)**

# BOM
| Name of item | Description | Subsystem | Part Number | Manufacturer | Quantity | Price | Total |
|---|---|---|---|---|---|---|---|
|Terminal Block Relay|24V AC/DC Input, DIN Rail Mount| Safety | X766842 | ASI | 2 | $11.96 | $23.92|
|SensaGuard 440N-Z21SS2A|Non-contact switch| Safety | 440NZ21SS2A | ALLEN-BRADLEY | 3 | $155.01 | $465.03|
| **Total** |  |  |  | **Total Components** | 5 | **Total Cost** | $488.95 |

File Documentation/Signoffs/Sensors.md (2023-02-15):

# Sensors System 

## Subsystem Function  

The role of the sensor subsystem is to send signals—communicating the status of the device occupancy of the presently forefront compartment sections on all three dial layers—to the PLC to update certain tags, so that the PLC's ladder logic code can properly use that information ad hoc.   

## Constraints  

**The Sensor System:** 

* **1. Cannot take up more than eight input pins from the PLC**    

   ^The Siemens PLC module S7-1200 has fourteen input pins of which six have already been designated to inputs from other systems.

* **2. The distance sensor chosen must determine the presence or absence of a device by measuring whether the light emitted was reflected back from a distance range of 3.75 to 7.25 inches** 

   ^The minimum distance a device will be from the sensor is 3.75 inches, and the maximum distance a device will be positioned from the sensor is 7.25 inches.

   ^The sensor must not sense up more than a distance of 11.25 inches; this is the length of the compartment and the closest the sensor will be to the dial. This is to     prevent mistakenly sensing the back wall of the compartment as a device. 

* **3. Must send a one signal to the PLC if there is a device in the presently forefront compartment section and a zero signal if there is not.**  

   ^This constraint is chosen when considering the consequences in the case of the wire being cut: 

If the default (zero) signal communicates that a device is present then the door could be able to be opened, upon someone trying to check a device out, because         the PLC thinks there is a device there to be distributed. 

If the default (zero) signal communicates that a device is not present then the door will remain locked and cannot be unlocked because the PLC thinks there is no       device there to distribute. 

Upon reflection the second option is the best because the devices are protected behind the locked door which will prevent theft during the time period before the       wire connection is fixed. 

* **4. The sensor must be mounted in the space of 3.75in. by 6in. by 0.75in that is between the door and compartment**

   ^The area floor space between the door and the compartment is 3.75x6.00 inches
   ^The height from the floor space to the bottom of the door is 0.75 inches

## Schematic  

SensorSchemTwo

SensorCloseUp

Each sensor possesses three wires; the power and neutral wires are connected to the power system, and the signal wires are connected to the PLC system.

SensorPosition1

SensorPosition2

SensorPosition3

SensorPosition4

SensorPosition5

The sensor has two thredded holes to mount onto the floor using screws right below the door with the emitter and receiver elements pointing towards the door. The sensor can be moved up to three inches closer to the compartment if needed to satisfy the distance range constraint.

## Analysis  

**Constraint 1 - Input Pins**

Using three ifm spot sensors with one bit signals will only take up three I/O pins on our PLC, which is less than the maximum of eight allowed.

**Constraint 2 - Distance Sensing Range**

Our chosen sensor measures up to a range of 0.60 inches to 7.87 inches; this will cover the 7.25 inch maximum distance requirement; this will also cover the 3.75 inch minimum distance requirement.
The sensor is not capable of sensing the back wall because it is 11.50 inches from the beginning of the compartment which is out of the sensors range.
The background suppression of the sensor also could be used to not sense the back wall.

**Constraint 3 - Signaling**

Our chosen sensor has negative and positive switching on the output signal, therefore the sensor is capacble of sending a positive output signal if it senses an object and a negative output signal if it does not sense an object.

The sensor can be connected electrically to the power and PLC systems through the ifm OGH580 connector cord.

**Constraint 4 - Sufficient Space and Mounting**

The length of the sensor, 2.07 inches, suffices the 6.0 inch maximum.
The width of the sensor, 1.40 inches, suffices the 3.75 inch maximum.
The height of the sensor, 0.75 inches, suffices the 0.75 inch maximum.

The OGH580 has two threaded holes to screw the sensor into the floor plate to mount.

## BOM  

| Name of item | Description | Subsystem | Part Number | Manufacturer | Quantity | Price | Total |
|---|---|---|---|---|---|---|---|
| OGH580 | Diffuse Reflection sensor with background suppression | Sensors | OGH-FPKG/US/CUBE  | ifm Efector inc. | 3 | $109.00 | $327.00 |
| EVC001 | Female Cord set | Sensors | ADOGH040MSS0002H04 | ifm Efector inc | 3 | $11.50 | $34.50 |
| **Total** |  |  |  | **Total Components** | 6 | **Total Cost** | $361.50 |

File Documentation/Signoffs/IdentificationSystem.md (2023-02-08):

# Identification Subsystem  

## Subsystem Function  

This Subsystem's role in the team's design is to scan barcodes on school devices before being placed and when being taken from the machine. The subsystem also includes a RFID Card Reader to verify and store students' identity. The PC will then receive information from the modules and store information in a database for our customer. The Windows PC will also be able to control the visual components like LEDs through a PLC.

## Constraints  

#### Constraints are numbered from C1 to C9 ####  

* Barcode Scanners shall be low power and consume no greater than 5 V 0.5 A. This is due to being powered by the PC. Common computers only output a max rating of 5 V 0.5 A.  
^ Source: https://resources.pcb.cadence.com/blog/2020-what-are-the-maximum-power-output-and-data-transfer-rates-for-the-usb-standards  

* Barcode Scanners shall be able to decode Code-128 barcodes 

* Barcodes shall be of decent quality to follow ISO 15416 standard. Assures that the codes can be read by any scanner  

* RFID Card Scanner shall be low power and consume no greater than 5 V 0.5 A   

* RFID Card Scanner shall operate on 13.56 MHz commonly used for higher security access badges, like the school Eagle Cards  

* A Barcode Scanner and Card Reader will be monitered by USB voltmeter to ensure correct operation  

* The PC shall run on Windows 10 to provide the needed applications for PLC and Database

* The PC will provide an ethernet port to communicate with the PLC through a USB NIC (network interface card)  

* The PC will provide at minimum an Intel Core i5-8400H or stronger CPU and 16GB RAM to support PLC programs

## Schematic  

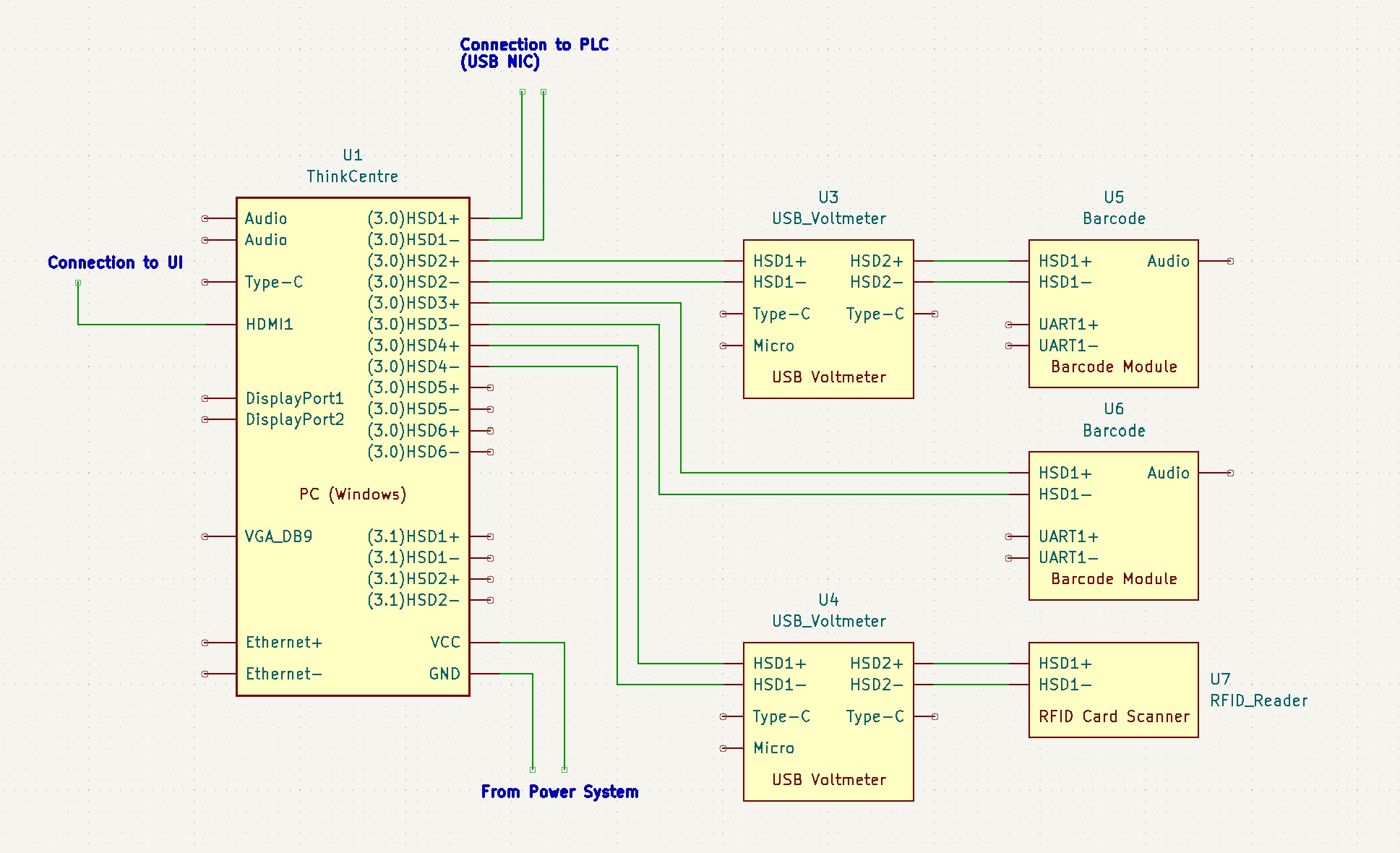
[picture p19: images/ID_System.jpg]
Schematic
    

The Schematic above shows the layout of the ID subsystem. The PC (U1) connects to the PLC through a USB NIC, which is a USB to ethernet adapter, and is powered by the power subsystem. The PC is connected to and allows for multiple modules through six USB 3.0 ports. Two USB Voltmeters (U3,U4) are used for a Barcode Scanner (U5) and RFID Reader (U7). The UI system is connected to the PC through the HDMI on the PC.  

## Analysis  

### Constraint C1-C3 ###  

The chosen barcode scanner is specified to read 1D and 2D barcodes, and supports reading a Code 128 barcode. The listed operating voltage of the barcode scanner is 5 V and the operating current is 135 mA. Both specs fall within the allowable amount of a common computer USB port. The standby current is better sitting at 58 mA, the module is made to communicate through USB and UART, and the scanner can be programmed to view vertically and horizontally. The scanner operates in 0 to 60 degrees Celsius, which will work since the machine should be in room temp, around 20 degrees Celsius. Barcodes for devices can be created online via free sites such as the site: https://www.barcode-generator.org/.   

^ Source: https://www.waveshare.com/w/upload/d/dd/Barcode_Scanner_Module_Setting_Manual_EN.pdf  

The barcode scanner will be used at different ranges to determine an appropriate range for a box to be placed and still be correctly read. To verify the code information, the scanner output will be compared with the expected outcome to ensure a box is not mislabeled. There will be 2 barcode scanners. One will be placed inside the machine so boxes can be loaded. Another will be outside the machine with the RFID reader to scan when a student gets a box. All the modules will be fed through a usb hub. 

### Constraint C4-C5 ###  

The RFID scanner is specified to function on a 5V, 100mA supply through USB. This is in line with the appropriate supply given through USB by the ThinkCentre computer. The module is verified to work with Windows 10 and is able to act as a serial port that sends in the first 8 Hex numbers of a card. The scanner is specified to work on 13.56 MHz frequency cards, which is what software in our phone can read. A phone can pick up an ID card, so 13.56 MHz should be the correct frequency for Eagle Cards.     
### Constraint C6 ###  

To verify correct hardware operation of the barcode scanner and the RFID reader, a USB voltmeter will be used connecting the scanners to the PC. This will allow the team to monitor the scanner during operation, ensure the 5 V 0.5 A limit is not exceeded, and the scanners operate at the correct standby current. The current USB voltmeter in mind is the 2 in 1 USB micro and type C connector and the scanner is the Waveshare USB scanner module that will work along the PC. The voltmeter is able to monitor the Voltage and Current taken by the Module. A benefit of the meter is the ability to verify operating current and voltage when a box is scanned. The meter has other functions such as temperature measurement to make sure the parts operate in the correct range. Other functions are measuring Power, resistance, capacitance, showing graphs of usage, and giving warnings if the limits of the meter have been exceeded. The meter is rated to handle devices like phones that are connected to mains, so it should be safe to use with a module connected to a computer.    

To remove data from the computer for use, a backup program will be added to the PC so when the drive is plugged in, the information is downloaded automatically. The port will be behind a locked compartment so students cannot access the data.  

### Constraint C7-C9 ###  

To connect the Computer to the PLC, a USB NIC will be needed to provide an extra Ethernet port. The PLC uses Profinet, which is a communication protocol used to collect information and control a PLC through Profibus. The Computer will run on Windows 10 and allow use of an application called TIA Portal. TIA portal allows connection to the PLC and functions as a programmer for the S7 1200 and 1500 series. To use the TIA portal software, the PLC needs a minimum of 16 GB of RAM and an Intel Core i5-8400H or stronger CPU. The ThinkCentre provides enough RAM and a strong enough CPU to handle the program. The program will be created in the TIA portal and loaded to the memory on the PLC. TIA portal also provides diagnostics of the PLC through the software. The PLC the team is using is called a SIMATIC S7 1200 from Siemens and requires certain types of memory card. The three options of memory for the PLC differ only by capacity. The three options for memory size are 2, 4, and 24 MB. The team is using a 4MB memory card for the PLC since the 2MB is out of production. Issues have arrived with a USB NIC not being recognized by TIA Portal. If the software does not recognize the NIC, the way to fix the issue is to enter the IP address manually. The TIA Portal SIMATIC Step 7 program allows the activation of an OPC UA Server built into the PLC which will allow communication.  

^ Source: https://us.profinet.com/profinet-explained/, https://support.industry.siemens.com/cs/document/109784439/delivery-release-simatic-step-7-professional-basic-v17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  

To retain information from the PLC and PC, an OPC UA client from Prosys will be used. The OPC client allows the PLC to connect and send/receive data to/from the database. The database will be accessible to the PC as well. The database will be the interface between the PC and PLC. The PC will be able to set bits high to activate the PLC, and the PLC will be able to set the bits low after completion of the job. The OPC client is designed to be used with SIMATIC S7 1200 and 1500 series PLCs, and connect to the MySQL database software. The Prosys OPC client can connect directly to the Server created in the TIA portal software and then relay the information to the database for use by the PC and vice versa.  

^ Source: https://downloads.prosysopc.com/opcua/apps/JavaClient/dist/3.2.0-328/Prosys_OPC_UA_Client_UserManual.pdf  

## BOM  

| Name of item | Description | Subsystem | Manufacturer/Part# | Quantity | Price | Total |
|---|---|---|---|---|---|---|
| Eversame 2 in 1 USB Tester | Voltmeter | Identification System | Eversame | 2 | $22.99 | $45.98 |  
| Barcode Scanner Module | 1D/2D Code Reader | Identification System | Waveshare | 2 | $39.99 | $79.98 |  
| RFID Reader | 13.56 MHz card reader | Identification System | Vipxyc | 1 | $14.99 | $14.99 |  
| ThinkCentre | Windows 10 Pro | Identification System | Lenovo | 1 | $759.00 | $759.00 | 
| USB Ethernet Adapter | USB NIC | Identification System | CableCreation | 1 | $15.99 | $15.99 |
| Siemens Memory Card | SIMATIC memory card | Identification System | Allied Electronics / 6ES7-954-8LC03-0AA0 | 1 | $90.96 | $90.96 |  
|  |  |  | **Components** | 8 | **Total Cost** | $1,006.90 |

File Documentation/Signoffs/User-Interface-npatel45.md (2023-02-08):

# Vending Machine Subsystem - User-Interface
### Function of the Subsystem:
---
When designing vending machine the main component of the machine is to get input from the user and process that information and send that information to the rest of the parts corresponding to it. So, in the same way for ECE board vending machine the student must be able to input their information, and select products from given set of  choices so to target this requirement, UI (User Interface) subsystem is required.
 
### Specifications & Constraints:
---
 
  1. UI must not operate at greater than 100 W because of PC output rating of USB-C [1].
  2. UI must run Windows/Linux environment to run Kiosk application.
  3. Must have HDMI or type C or USB port to connect to PC.
  4. UI must be at least 15.6" (diagonal) because of the TIA (Totally Integrated Automation) Portal application.
  5. UI must be anchored to prevent theft problems.
### Schematic:
---

<div align="center">  
  

  
_Figure 1: Dimensions of LCD [2]_
  

  
_Figure 2: Ports on LCD [2]_
 

  
_Figure 3: Possible Connections of LCD with PC [2]_


  
_Figure 4: Schematic of the System_

<div align="left"> 

### Analysis:
---
 
The vending machines' main interface with the students will be the LCD. It will be utilized for student feedback as well as for displaying information to students, such as messages about devices. Therefore, it will need to be touchscreen. There are two main types of touchscreens that are available: Resistive and Capacitive. 
 
#### 1) Resistive Touchscreen [3]
  
The fundamental components of a resistive touch screen are two substrate layers that are spaced apart by either an inert gas or air. For the top layer, a flexible film-based substrate is always used, however for the bottom layers, either film or glass may be used as the substrate. On the inner-facing surfaces of the substrate layers, opposite the air gap, a conductive substance is deposited. There are only two operational states for a resistive touch screen: touched and not touched. The conductive substance on the top layer makes electrical contact with the conducting surface of the bottom layer when a user presses down on the top surface, indenting the film in the process. This action generates a voltage differential that the system interprets as a touch. The touch controller analyzes the action after determining the precise X and Y coordinates of this contact. A resistive touch screen is like a mechanical switch as it requires physical force to operate.
  
<div align="center"> 


 
 _Figure 5: Working of Resistive Touchscreen [4]_
  
 <div align="left"> 
   
  - Pros
    - Low Cost
    - Less possibility of accidental contact
    - Can detect any object when properly pressure
    - Expensive compared to resistive touchscreen
    - Higher sensor resolution
- Cons
    - Unable to react to multiple-touch sensing
    - Less sensitive, and as a result, requires pressure to function.
    - Lower display clarity is caused by a thick top layer.
    - The screen is more vulnerable to scuffing and scratches.
    - Expensive to fix
    - If the screen has a minor fracture, it won't function.

#### 2) Capacitive Touchscreen [3]
  
The base of capacitive touch panels is a collection of conductors that generate an electromagnetic field. The user's conductive finger or object pulls or adds charge to the capacitive field, adjusting its strength, as they touch the screen. Based on the sort of input it receives, a touch controller measures the position of this change and then orders the system to do a certain action. Users only need to tap a capacitive touch screen for a device to recognize their input. Contrary to resistive touch displays, there is no need for physical pressure. Capacitive touch screens can support a variety of inputs, with varied motions and additional contact points instructing the system to execute a variety of actions, which is another important distinction from resistive touch technology.
     
<div align="center"> 
 


 _Figure 6: Working of Capacitive Touchscreen [4]_
  
 <div align="left"> 
  
 - Pros
    - Durability
    - Facilitates Customization
    - Offers functions for multiple-touch sensing.
    - Easy to Clean
 - Cons
    - Expensive compared to resistive touchscreen
    - Because it is highly sensitive, even the slightest touch can cause it to activate, which could result in inadvertent contact.

It is evident from the finding that Capacitive touch screens outperform resistive touch displays in a variety of ways. Although more expensive, capacitive touch displays offer advantages that surpass the price, making them the better choice. Additionally, since it is used for user input and to meet the constaint #4 of running TIA (Totally Integrated Application) portal the LCD has to meet the 15.6" diagonal display measurement. Also,since the LCD only need power a little more than 10 W and the PC can provide more than what is needed,it satisifes the constraint #1.Additionally, since the PC supports USB-C (Universal Serial Bus) our team has decided that a USB-C interface would work better because of two main reasons (satisifies Constraint #3):-
 
 1. The USB Type-C port would be used to supply the LCD with the power it needs (from PC).
 
 2. Type-C offers a single interface for both power and signal. As a result, it reduces noise and avoids using two cords.
  
 Additonally, since the PC (ThinkCentre) that our team is going to proceed with supports Windows, and the LCD does get along with that satisfies constraint #2.And, to finally prevent LCD from getting stolen it will be mounted on wall or on top of machine using a Touch Nexus stand.
  
 So to meet all the above requirements the following decision was made:

<div align="center"> 
  
| | Details |
|:---:|:---:|
| Name/Brand | View Sonic 15.6" Touch Screen LCD |
| LCD Type | IPS (In Plane Switching Technology) |
| Touchscreen | Yes (Can also be used as external monitor through HDMI) |
| Type | Projective Capacitive |
| Interface | USB Type-C/Mini-HDMI |
| Diagonal Size | 15.6" |
| Consumption | 8.6 W (Typical) 10.5 W (Max) |
| Documentation | Good |
| Mount Stand | Touch Nexus |

<div align="left">
  
### BOM (Bill of Materials): 
---
  
<div align="center">
 
| Part | Price |
|:---:|:---:|
| ViewSonic LCD | $ 269.99 |
| USB-C to USB-C cable  | (-) Included |
| USB-C to USB-A cable  | (-) Included |
| Mini-HDMI cable | (-) Included |
| Passive Touch Pen | (-) Included |
| Touch Nexus Stand | $89.95 | 
| **Total** | **$359.94** |
 
<div align="left">
  
**Link to the product:**   
  
[1] https://www.bestbuy.com/site/viewsonic-15-6-lcd-fhd-monitor-displayport-vga-usb-hdmi/6428015.p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
 
[2] https://www.viewsonic.com/us/td1655-15-6-portable-1080p-ips-touch-monitor-with-60w-usb-c-and-mini-hdmi.html
 
[3] https://www.bosstab.com/tablet-stands/touch/nexus-wall-mount/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

### References: 
---
[1]. https://manhattanproducts.eu/pages/usb-c-pd-charging-everything-you-need-to-know
  
[2]. https://www.viewsonic.com/us/td1655-15-6-portable-1080p-ips-touch-monitor-with-60w-usb-c-and-mini-hdmi.html
 
[3]. https://forum.digikey.com/t/resistive-touch-vs-capacitive-touch-whats-the-difference/1063
  
[4]. https://www.researchgate.net/publication/356667592_Fabrication_and_Performance_Evolution_of_AgNP_Interdigitated_Electrode_Touch_Sensor_for_Automotive_Infotainment

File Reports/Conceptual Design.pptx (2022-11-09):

## Team 5 Conceptual Design

- Dillon Williams
- Nidhay Patel
- Ryan Reed
- Michel Turpeau
- Austin Sigg

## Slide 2

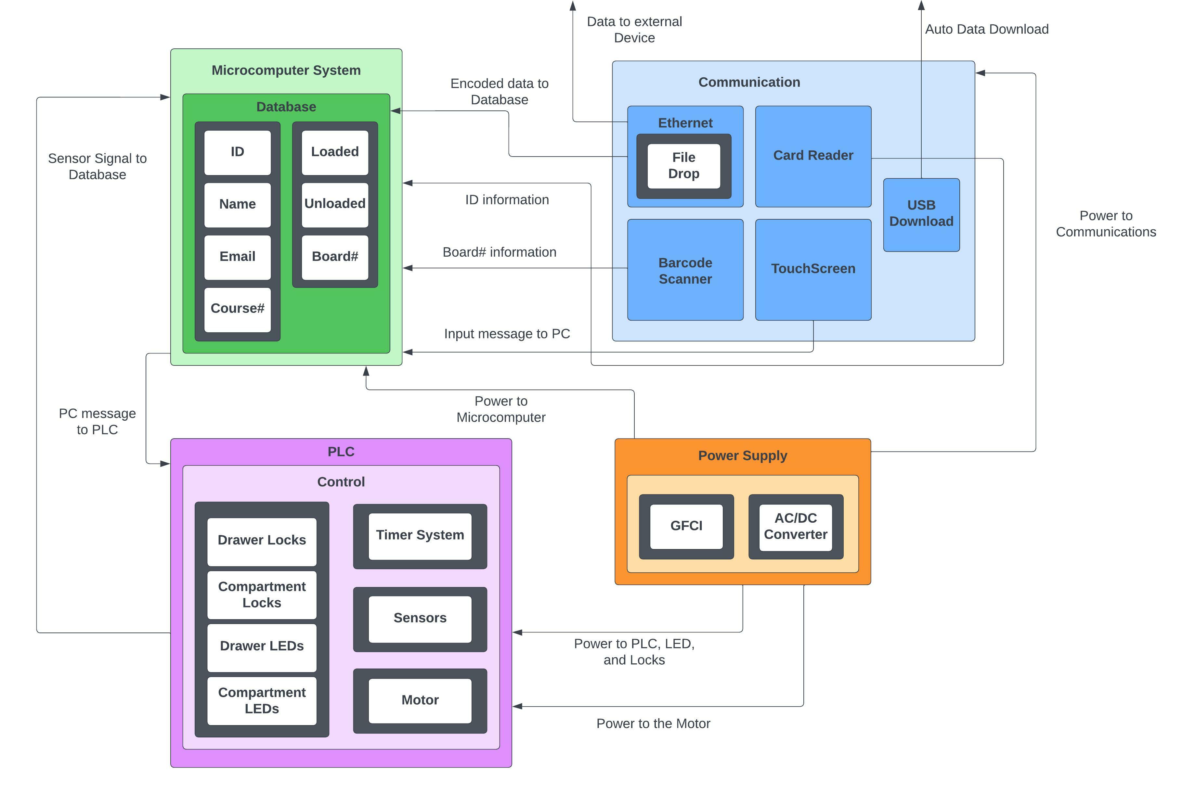
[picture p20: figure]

## Microcontroller

- Raspberry Pi Model 4 B
  - Card Reader
    - Input: Signal/Message/Information from Eagle Card
    - Output: Create Data and signal Microcontroller Unit
  - UI
    - Raspberry Pi LCD touchscreen
      - Input: Information from Student
      - Output: Raspberry Pi signaling PLC

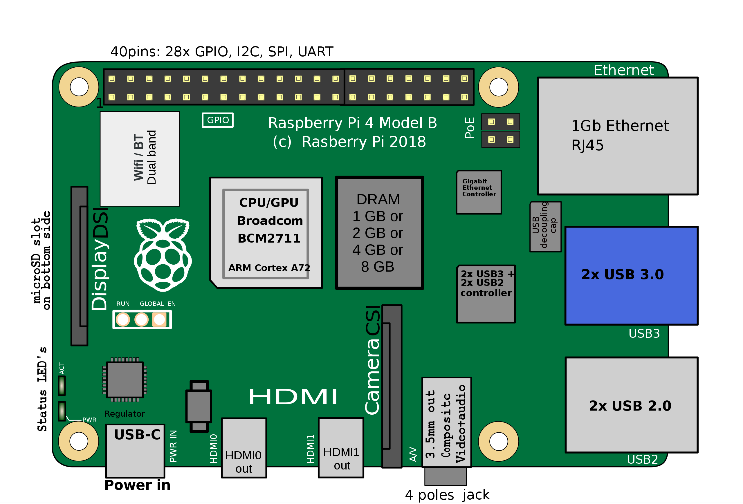
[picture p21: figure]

## PC connections

- miniPC
1. SQL Database
2. Touchscreen
3. Eagle Card Reader
4. Ethernet
5. USB

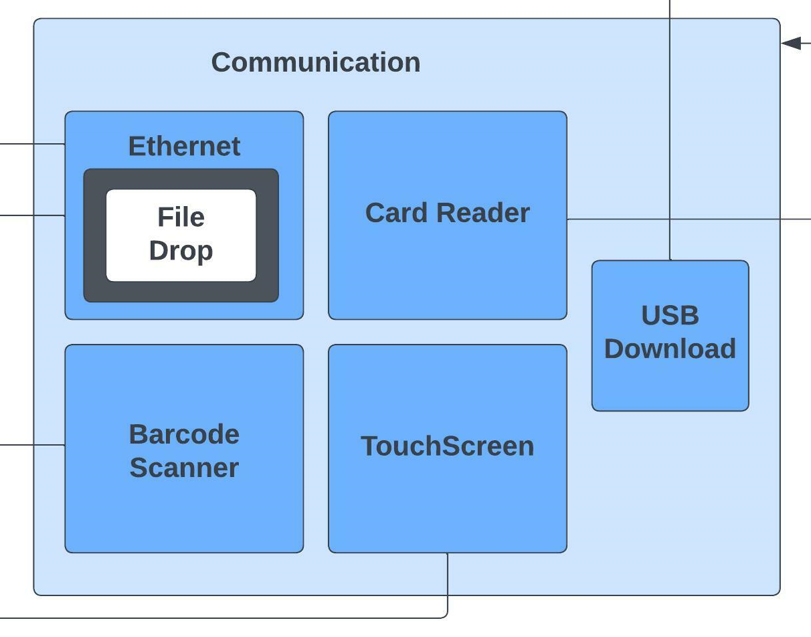
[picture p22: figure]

## SQL Database

- Inventory
  - Loaded
  - Unloaded
- Student Information
  - T#
  - Name
  - Email
  - Course & Board#
- Ethernet
  - CSV File

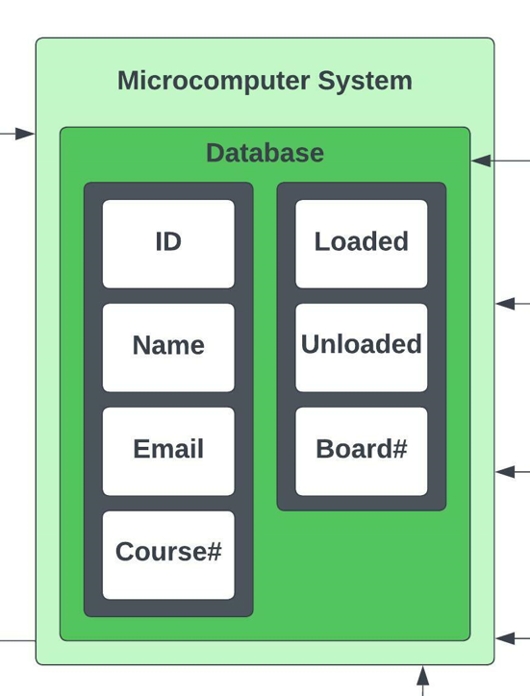
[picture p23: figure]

## Constraints

USB

- Be able to automatically transfer data to the faculty’s thumb drive when inserted into the machine

- Database

- Have a created Schema available and have a server to contain the student data and Schema itself

- Card Scanner

- Be able to read data from Eagle Cards and store the identifier in the database for faculty use

## Hardware connections

- PLC
- HW Control
  1. Locks
  2. Indication
  3. Timer System
  4. Sensors (Addressed later)
  5. Motor

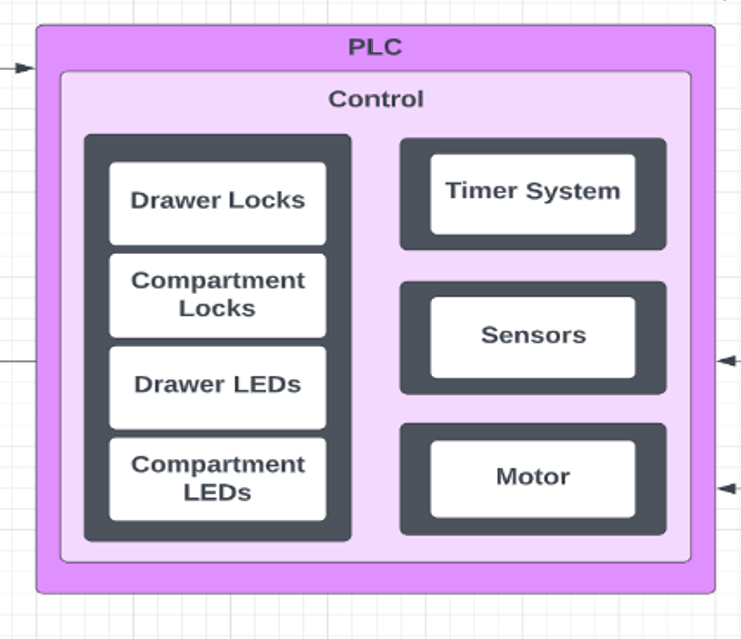
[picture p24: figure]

## Why a plc & a microcomputer?

- PLC’s “run-to-completion” step is Cycle-Driven!
  - Will always scan its code on a given interval (ex. every 100ms)
  - A microcomputer is event-driven: will complete its scan once an event is activated
    - Could be SIGNIFICANTLY longer
- PLCs are used in industry specifically for control technology
  - Almost all hardware in industry can be easily controlled by PLCs
  - Makes controlling fewer components much more simple
- If PLCs can do this, why not use it for a database?
  - PLCs aren’t good with sharing a lot of data, except for HMIs and DAQs
  - Can’t understand SQL

## Plc Control / Hardware

- PLC Constraints
  - ii(1) Must interface with the locks and LEDs
  - ii(2) Must control the step voltage of the motor(s)
  - ii(3) Must communicate with the microcomputer
  - ii(4) Must know the device occupancy of each drawer
  - ii(5) Must have a timer system

- Hardware
  - PLC receives power from wall outlet
  - Hardware receives all control from the PLC
  - Sensors, Locks, Timer System, Indication System, Motor

## Hardware subsystems

- Stepper Motor
  - PLC will control driver for motor
  - Motor steps enough degrees to rotate new device to drawer
- Locks
  - Most likely solenoid (Proposed by MechE team)
  - Powered by DC voltage

- Indication System
  - Most likely LEDs. Will help guide student to correct drawer and compartment
  - Controlled by PLC
- Timer System
  - Used to flash LEDs and unlock compartments over a predetermined duration
  - Controlled by PLC
  - Will be a system to alternate TON timers

## Explanation for Stepper Motor

## Locks

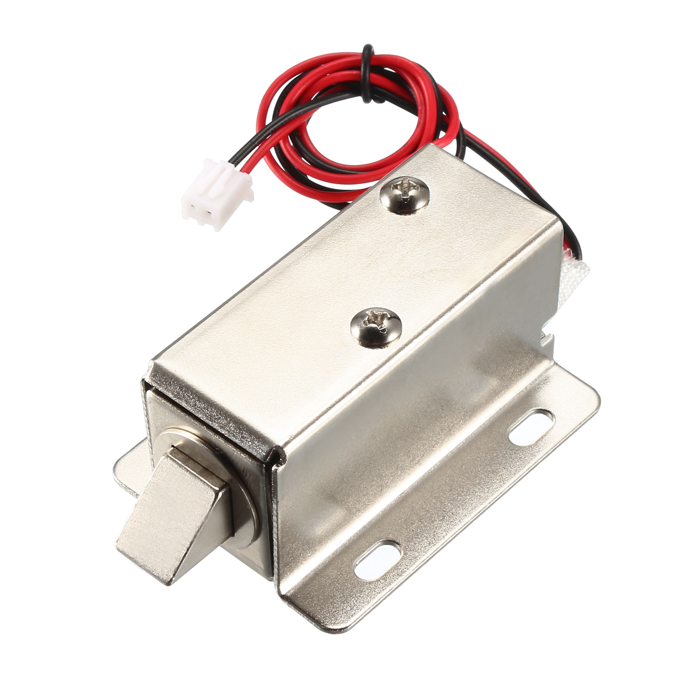
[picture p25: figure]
See the source image

- Main security for the physical system.
- Locks for each of the drawer, and for each of the compartments.
- The drawers will require more strength, since they are directly exposed and easy to grab a hold of.
- Needs to stay lock when power is lost.

## LEDs and Indicators

- To assist the user, both the operator and the consumer, there will be a series of LED indicators guiding them to the designated compartment.
- User Mode (For Consumer):
  - After successfully completing the rental process the LED will flash, indicating the drawer and the compartment that the item is stored.
  - Once the item is removed and the compartment and drawer are closed, the LEDs turn off.

## Barcode Scanner

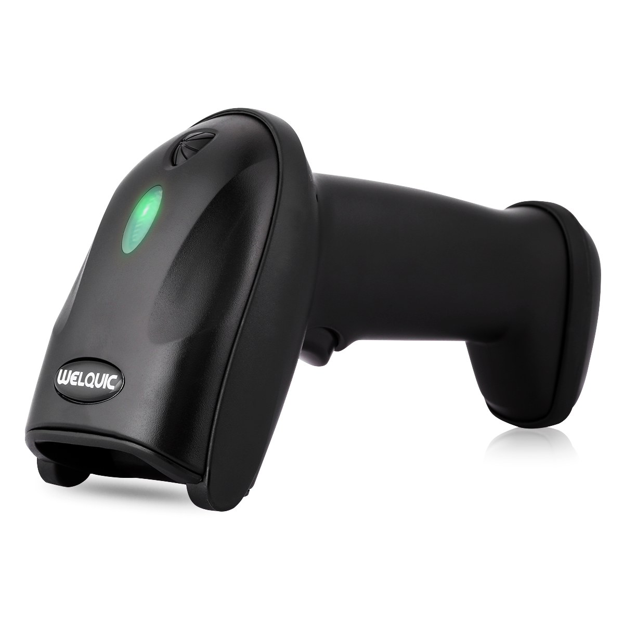
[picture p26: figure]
See the source image

- Used to scan in the ID/barcode attached to the device’s box.
- Makes it easy to keep track of items have been registered to the database.
- Will be used by the operator during the “LOAD” mode.

## LOAD Mode

- Mode loading and registering items to the machine.
- The machine is aware of empty compartment.
- LED indicators will inform the user of the compartment that needs a new item. (The only ones unlocked)
- The user CANNOT move on to the next drawer until they have scanned in the device and loaded it into its compartment.

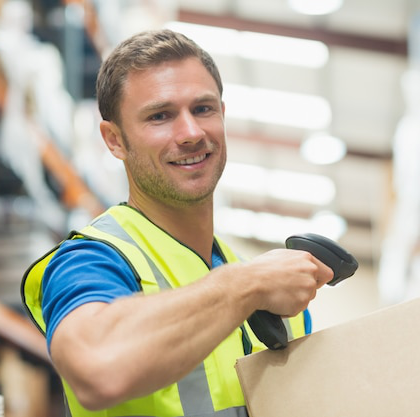
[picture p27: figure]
See the source image

## Power

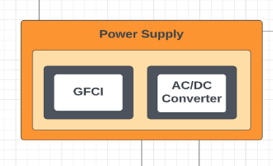
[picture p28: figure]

Constraints:
iv(1) As per the standard NEC 422.51, the power system must have a ground fault current interrupter (GFCI) to protect against the current surge.
iv(2) The power system must have an AC/DC converter to send power to the voltage-sensitive components.
iv(3) The power system must have an emergency stop control.

- Power Supply
- AC/DC Converter
- Overcurrent Protection
  - GFCI-protected outlet
    - NEC 422.51
    - Circuit Breaker
    - Fuses
- Op-Amp Circuits

## Systems that require Power


- Microcomputer
- PLC
- Motor
- LEDs
- Locks
- Barcode Scanner
- Card Reader

## Sensors

Photo Eye Sensor | How to Wire a Photoelectric Sensor into a CompactLogix Allen Bradley PLC
HC-SR04 Ultrasonic Distance Sensor - SparkFun | Mouser

- To determine occupancy of each compartment
- Hundreds of options to consider
- Ideals
  - Small Size
  - One bit output
  - Cheap
  - Easy Calibration

Constraints:
iii(4) The PLC must know the device occupancy of each drawer.

Amazon.com: uxcell 100kg 42mmx38mmx3mm Electronic Scale Body Load Cell Weighing Sensor for Kitchen Scale,Human Body Bathroom Scale, Jewelry Scale : Home & Kitchen

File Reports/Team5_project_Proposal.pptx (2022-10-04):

## Team 5 project Proposal

Dillon Williams, Ryan Reed, Austin Sigg, Nidhay Patel, Michel turpeau

## Project Overview

- nidhay

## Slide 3

- Nidhay – mainly background and the objective

## Specifications and standards

- dillon

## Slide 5

- dillon

## Existing Solutions


Elevator Vending Machine
PROS:
- Safety of Devices
- Decent Inventory
CONS:
- Shelf Customization Decreases Inventory
- Machine Size (6’4”H x 4’7”L x 3’3”W)
PRICE:
Unknown, but generally > $3500

## Existing Solutions


Smart Vending Machine
PROS:
- Convenience is its Priority
- No Buttons = Less Jams
CONS:
- Low Safety for Higher Shelves
- Maintenance and Repairs
- Size as well (6’3”H x 3’10”L x 2’10”)
PRICE:
$2000 - $2350, some can reach $7000

## Existing Solutions


Lockerbox Array
PROS:
- Various Sized Boxes
- Locks for each device
CONS:
- Storage / Refilling
- Locks must have Strong Resistance
Price:
Unknown, generally

## Proposed Solution

- Ryan – systems (basic talk of what we want), unknowns, ways of testing systems, mention mechanical and what they think would work (Like Fastenal 3D array lockbox)

## Measures of Success

- austin

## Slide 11

- Austin – also impacts of the project

## Resources

- Michel - budget, timeline, conclusion area

## Timeline and Conclusion

- michel

## Questions?

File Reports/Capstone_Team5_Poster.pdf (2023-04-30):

Michel Turpeau, Austin Sigg, Ryan Reed, Dillon Williams,

# and Nidhay Patel

# Class Kit Vending Machine

# Abstract

# Design Requirements

# Experimentation

Typically, in the first month of a semester, students attempt to check out on average 50 devices in a day from the Office. This capstone project was focused on designing and implementing a vending machine that could distribute devices out to students while recording when students checked out a device. The ideal product would be a vending machine with the functionality to vend the needed specific devices to students.

The student enters information into the GUI using the given keyboard and cannot close or leave the application for any reason. The student enters their ID, name, email, which course is needed, and the term. Before the board can be rented, the information is checked for formatting errors and the student must agree to the listed terms. The GUI is connected to a SQL (structured query language) database storing all the data. After the data is verified, the machine reads the current position to assign the correct device to the student. The PLC receives the order to turn on the motor given the GUI state and the admin is allowed to delete information and load devices from the GUI given certain commands and passwords as well.

# System Communication

# Safety

# Power

- Separate from other systems
- Controls Relays
- Interrupts peripherals' power
- Intuitive & Simple UI
- Information Error-Checking
- Protects from SQL Injection
- Send/Receive PLC Data

# Software

- Houses 120V AC Driver which provides 24V DC output
- Provides protection to the team and students
- Built in GFCI protection

The team was able to get most of the major systems operational. The biggest concern was the safety of student data and the integrity of the Database. To protect the database, the team needed to have a combination of buttons to shut down the program and needed to prevent SQL injection into the program. The information stored was kept offline so the computer could not be accessed through another device and the code contained input validation so no other type of information could be entered. An image of the GUI is below. As for the other systems, the Safety sensors were able to interrupt the power sent to peripherals if the door was open, the Power system was able to power the Motor through an enclosure, and the GUI was intuitive and simple in design. The PLC average current consumption is also below and does not exceed the rated value.

# Future Work

- Implement a barcode scanner and ID card reader to avoid students entering the incorrect T# in the database
- Fully implement the power system to be independent from the current configuration
- Add the locks into the machine and add functionality for the locks to the PLC
- Acquire Memory Card for Donated PLC

# Housing

# Acknowledgements

We are grateful to the faculty, staff, and Dr. Jesse Roberts here at Tennessee Tech for allowing our team to work on this project. We would also like to thank our Mechanical Team for their work on the housing of the machine.

# More Information

For more information on the project, you can check out our GitHub at: https://github.com/DillonSW/Capstone_Team_5.git

# Motor Schematic

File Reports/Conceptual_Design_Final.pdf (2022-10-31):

# Class Kit Vending Machine Conceptual Design

Nidhay Patel
Department of Electrical and Computer Engineering
Tennessee Technological University Cookeville, United States of America npatel45@tntech.edu

Austin Sigg
Department of Electrical and Computer Engineering
Tennessee Technological University Cookeville, United States of America aesigg42@tntech.edu

Dillon Williams
Department of Electrical and Computer Engineering
Tennessee Technological University Cookeville, United States of America dswilliams42@tntech.edu

Ryan Reed
Department of Electrical and Computer Engineering
Tennessee Technological University Cookeville, United States of America rcreed42@tntech.edu

Michel Turpeau
Department of Electrical and Computer Engineering
Tennessee Technological University Cookeville, United States of America mmturpeau42@tntech.edu
I. INTRODUCTION
Around fifty devices a day are needed by students each year for their ECE (Electrical and Computer Engineering) courses. The main emphasis of this capstone project is the design and implementation of a vending machine that can loan out devices to students while keeping track of which students have taken the devices. A student can enter their information into the machine, and it will keep track of who has borrowed each device(s). Students will be able to view and choose which gadget to remove with the help of an LED (Light Emitting Diode) equipped drawer system. The purpose of this step in the design process is to complete the following: detail what subsystems must be in place in order for the vending machine to run, how these subsystems will interact with each other, and finally, what constraints each subsystem will have imposed on it and how each constraint can be tested. The following is a numbered list of specifications that are then discussed in the later paragraphs.
1. The machine shall be 2 to 4 feet in height.
2. The machine shall use encrypted ethernet for data transfer
3. A Microcomputer/PC shall be used to manage the data and allow proper function
4. The devices shall be uniquely identifiable
5. The machine shall use a card reader to obtain identification
6. The machine shall have nonvolatile memory to store the programs and data
7. The machine shall have LED (light emitting diode) indicators
8. Locks shall be installed to prevent device theft
9. The machine shall allow auto-download of data given a USB drive
10. The machine shall have a motorized center in order to rotate which device should be taken.

The machine will be no taller than the average window height, which is around 2 to 4 feet, and no smaller than 2 feet in height. This allows for easy portability from the office to the student lounge at Brown Hall and vice versa. The machine will use ethernet to send data to our customers and be encrypted to avoid others from accessing the students’ information as well.

A Microcomputer (PC) will be used to manage the data acquisition system and allow the proper function of the machine. An SQL (structured query language) database will be programmed into the Microcomputer to hold the student ID (identification) number, name, email, course, and which board has been rented, as required by the customer. The boxes the devices are held inside must be uniquely identifiable according to the department, so each box must be scanned into the database before a device is taken. This is to prevent the theft of a device by any student and allows the customer to know which is taken. For the same reason, the machine shall have a card reader to ID every student. This way no student can fake the number, even if other information was incorrect.

For the entire machine to function after a reset and to remember information for the customer, the machine is required to have a form of nonvolatile memory such as MicroSD or an actual separate drive. The machine must have a series of LED indicators so the student knows which drawer and compartment to access when retrieving the board. Solenoid Locks shall be installed into the drawers and compartments so no single person can easily break through to the devices when the machine is unsupervised. The current plan is for a drawer and compartment to hold for several minutes to allow enough time for a worker to notice the attempt.

The following subsections provide detail on each of the previous requirements and how each shall be completed according to the customer.

II. BACKGROUND
A question that may arise from the conceptual design is: why use a PLC and a Microcomputer in the vending machine? One reason that a PLC is being considered is due to a PLC is cycle-based. When discussing execution schemes, there are two that can be used: event-driven execution and cycle-based execution. In an event-driven scheme, like a microcomputer, “a run-to-completion step is executed each time an event is raised,” while in a cycle-based scheme, like a PLC, “a run-to-completion step is executed periodically in regular time intervals,” [1]. The reason this needs to be addressed and specified is to show how a PLC can be useful in our design. Being event-driven, a microcomputer will wait to scan until input is sent to it. On the other hand, a PLC will constantly check all inputs and sensors on a certain time cycle. It’s important to have a cycle-based execution for the hardware components, such as locks and component sensors, because they are the main security measure against stealing the devices. There is a chance that if this scanning is done by the microcomputer, it could execute at the end of a long command, such as a “for” loop. If this is the case, the hardware scanning could happen minutes after the request was sent. Whereas if a PLC was used, the hardware could be monitored every scan cycle, for example, every 200ms. This makes PLCs more reliable in relation to securing the devices and monitoring hardware.

To secure the connection between the ECE office and the Vending Machine, there will be an encrypted Ethernet line. The form of encryption being used is called Symmetric cryptography [2]. This type of encryption allows both points of connection, Point A (The ECE Office) and Point B (The Vending Machine), to both encrypt and decrypt the information. This provides greater security than a simple Asymmetric system since both sides need a key to access the information.

To access information of the students who rented out the devices, a need for a database arises. For the database, a standard language is needed for accessing and manipulating the database. The chosen language for accessing the database is SQL [3]. SQL will be used to insert, retrieve and update information of the students who rented out devices.

III. ETHICAL CONSIDERATIONS
A scenario that must be considered is the stealing of a device from the vending machine. Given the chance that the faculty in the ECE office may step out of the office for a few minutes, there is a chance that someone could attempt to break into the vending machine to steal the devices within. To help prevent this, the vending machine will have locks on both the drawers and the lids of each device. There will also be a sensor system in place to detect if a box is in its compartment. While this will be mainly used for the SQL database, it can be given the purpose of detecting if a device is removed without approval.

A consideration that must be taken into account when designing this vending machine is the potential to take away jobs from ECE faculty. However, given why the machine is being designed and implemented, i.e. automating part of the process of checking out devices, the jobs of the ECE faculty will not be negatively affected. The ECE office faculty will have their jobs simplified by not having to keep track of paperwork, rather they will have a spreadsheet with student information and checked-out boards.

In addition, there will be a USB storage connection to transfer data to and from the device. This provides even greater security for the student data, that being physical security. This device will also require a form of encryption, in the case of misplacement or theft. The choice form of encryption would be one that can run directly off the USB drive, such as ‘Rohos Mini Drive’ or ‘VeraCrypt’ [4]. These types of programs use passwords, key files, and user varication to defend from capering. This would avoid the need for additional programs or applications to be installed on office devices.

IV. BLOCK DIAGRAM

A. Constraints
The following is the list of constraints that will be imposed on our subsystems:
i) Microcomputer System
(1) The microcomputer must contain a database that is programmed with SQL and another language such as C++ or Java.

ii) PLC

(1) The PLC must interface with the locks and
| LEDs.
(2) The PLC must control the step voltage of the
| motors.
(3) The PLC must communicate with the
| microcomputer.
(4) The PLC must know the device occupancy of
| each drawer.
(5) The PLC must have a timer system.

iii) Communication

(1) The machine must have a USB port to auto-
| transfer information between itself and the drive.
(2) The machine must receive a CSV file from the
| faculty computer.
(3) The Ethernet connection used to send the CSV
| file must have a form of encryption to secure student information.
(4) The machine must have a barcode scanner to
| send the board number to the microcomputer.
(5) The machine must use a card reader to read
| information off of an Eagle Card and use it as a unique ID.
(6) The machine must have a user interface
| involving a touchscreen to enter certain student information (such as name and email).


iv) Power System

(1) As per the standard NEC 422.51, the power system must have a ground fault current interrupter (GFCI) to protect against the current surge.
(2) The power system must have an AC/DC converter to send power to the voltage-sensitive components.
(3) The power system must have an emergency stop control.
B. Microcomputer System
The microcomputer system should be able to meet the following criteria: It should have enough storage to hold device information, student information, and programming. It should also have connectivity ports such as a USB (Universal Serial Bus) and an Ethernet port.

The Microcomputer will not only be used for keeping up with the Database but also be responsible for communication with other subsystem modules. It should comprehend input signals from the Card Reader, User Interface (UI), and barcode scanner. Also, it should communicate with PLC for carrying out the operation of vending devices.

The Microcomputer will be mainly used for the following functions:

1) SQL Database
a. Inventory
With the aid of a sensor in the PLC system, the database will be utilized to keep track of the inventory inside the machine and will be able to inform the client whether a device is loaded or unloaded. If the package is loaded, the system will verify that the barcode scanner has read it. The system will check to see if the box hasn't been

scanned and if it is unloaded. The database's inventory area will then be used to store and record all of the data.

b. Student Information

The database will also be used to maintain a list of the students who have borrowed gadgets for classes, and it will be able to transmit the data to the customer over Ethernet and/or a USB drive. The identification will be entered into the database under the students’ section using the card reader that is attached to the computer. A user interface will be used to input the student's name and email. From a list of courses the database has, a course portion will then be selected. The barcode of the chosen board will be read by the scanner once it has been selected, and the consumer will then be able to use it.

To validate whether the information has been correctly processed and stored in the database, a mock trial will be done by using a teammate’s Eagle card and after that, the data will be downloaded to see whether the information stored in the database is accurate or not. This will help verify that constraint i(1) has been satisfied and specifications 3 and 6 have been met.

C. PLC
In order to give the vending machine’s hardware reactive functionality, a PLC will be implemented along with its necessary sensors. The PLC will be able to message the

Figure 1. Block Diagram microcomputer as well in order for constraint ii(3) to be satisfied.
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

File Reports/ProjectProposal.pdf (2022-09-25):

# ECE Class Kit Vending Machine Project Proposal

Nidhay Patel
Department of Electrical and Computer Engineering
Tennessee Technological University Cookeville, United States of America npatel45@tntech.edu

Austin Sigg
Department of Electrical and Computer Engineering
Tennessee Technological University Cookeville, United States of America aesigg42@tntech.edu

Dillon Williams
Department of Electrical and Computer Engineering
Tennessee Technological University Cookeville, United States of America dswilliams42@tntech.edu

Ryan Reed
Department of Electrical and Computer Engineering
Tennessee Technological University Cookeville, United States of America rcreed42@tntech.edu

Michel Turpeau
Department of Electrical and Computer Engineering
Tennessee Technological University Cookeville, United States of America mmturpeau42@tntech.edu
I. INTRODUCTION
Every year hundreds of students require various devices for their ECE classes. These specific devices are provided by the College of Engineering and are rented out to students through the ECE office. Typically, in the first month of a semester, a considerable number of students attempt to check out these devices from the ECE office. This capstone project will focus on designing and implementing a vending machine that can distribute devices out to students while recording which students have checked out a device.

The finished product will be a vending machine with the functionality to vend the needed specific devices to students. A student can enter their information into the machine, and the machine will record who has checked out their respective device(s). The machine will have a transparent front, which will allow students to see and determine which device is the one they need. The student will then put in the correct input into the vending machine, and a platform will lift up to the desired device and bring it down to vend it to the student.

The ECE office will benefit from having this machine because it will reduce traffic in the ECE office. It will also ease the process for the students because they will not have to fill out the paperwork; The vending machine will allow the office to view the data submitted by the students. As a result of this new vending system, the office associates will not have to fill out paperwork on students as frequently, and the machine will remember the data that the students enter.

The first prototype of the vending machine will have the capability to prevent boards from getting stuck, have a touch interface for students to enter information on, have a locked door to enable associates to restock the machine, and have memory in the event of a fault or power loss: to remember its functionality. Also, the machine will be fitted with a method of communication for the associates to procure student information from it. Security will be implemented to prevent boards from being stolen and to protect the database.

The objective of this capstone project is to make the process of checking out required ECE course devices simpler by utilizing a vending machine, while also recording all information given by students through a database.

II. FORMULATING THE PROBLEM
This section will introduce the background information needed for the project. This includes the constraints of the machine, the specifications of the machine, and the standards we will be bound to while working on the project. A survey of viable solutions to the problem will also be given, so the project can be further improved in the future.
A. Background
The project relies a lot on the background information of the systems in vending machines and on how these systems operate. The project will require knowledge in the areas of controls, programming, embedded, power, databases, and various others.

Vending machines are used throughout many businesses and are a source of convenience for the customers who use them. The needed maintenance on well-made vending machines is also low: saving time and money for the business [1]. A vending machine for the distribution of class kits in the ECE office would be of great convenience to students who could now come by and pick up the device that they need with ease. It would eliminate the need to fill out the paperwork in the office required to obtain a board, and it would allow the office associates to do their own work without worrying about the students.
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

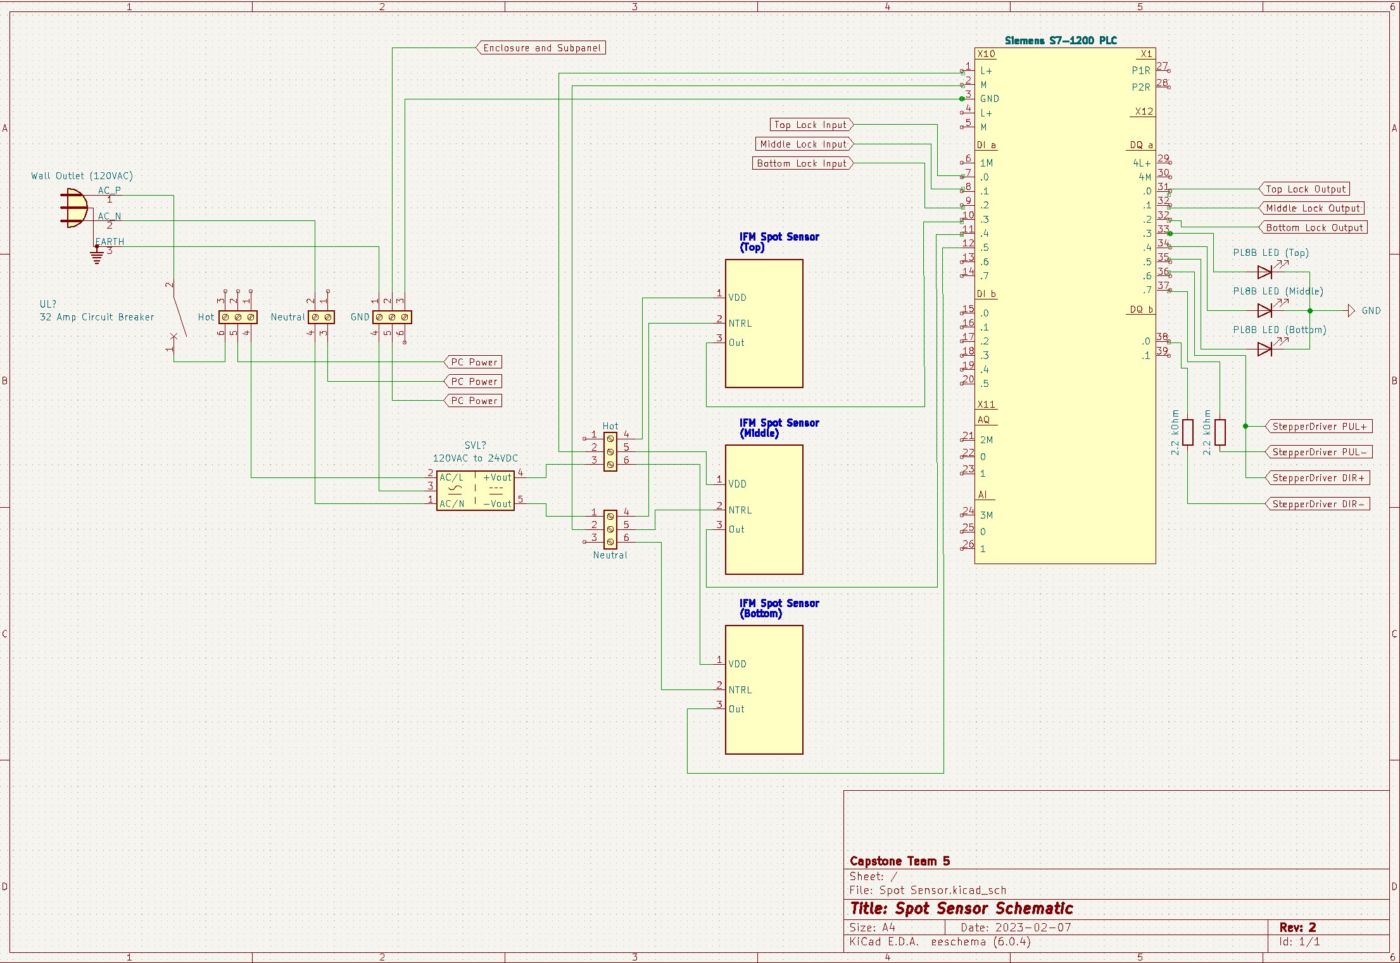
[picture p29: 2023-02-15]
Documentation/Images/Schematics/SensorSchemTwo.jpg

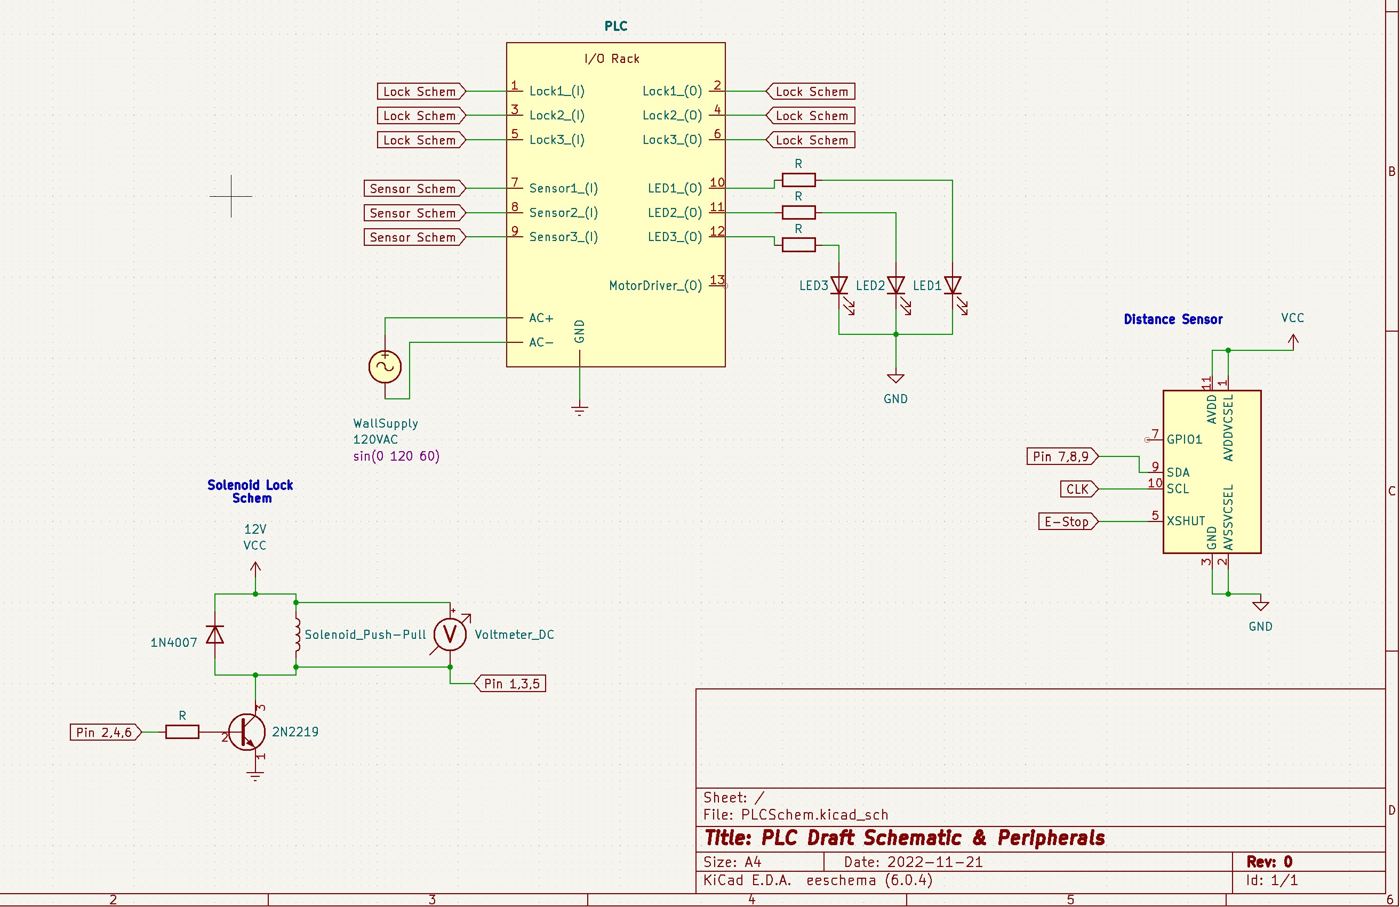
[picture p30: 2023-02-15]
Documentation/Images/Schematics/PLCSchematic.jpg

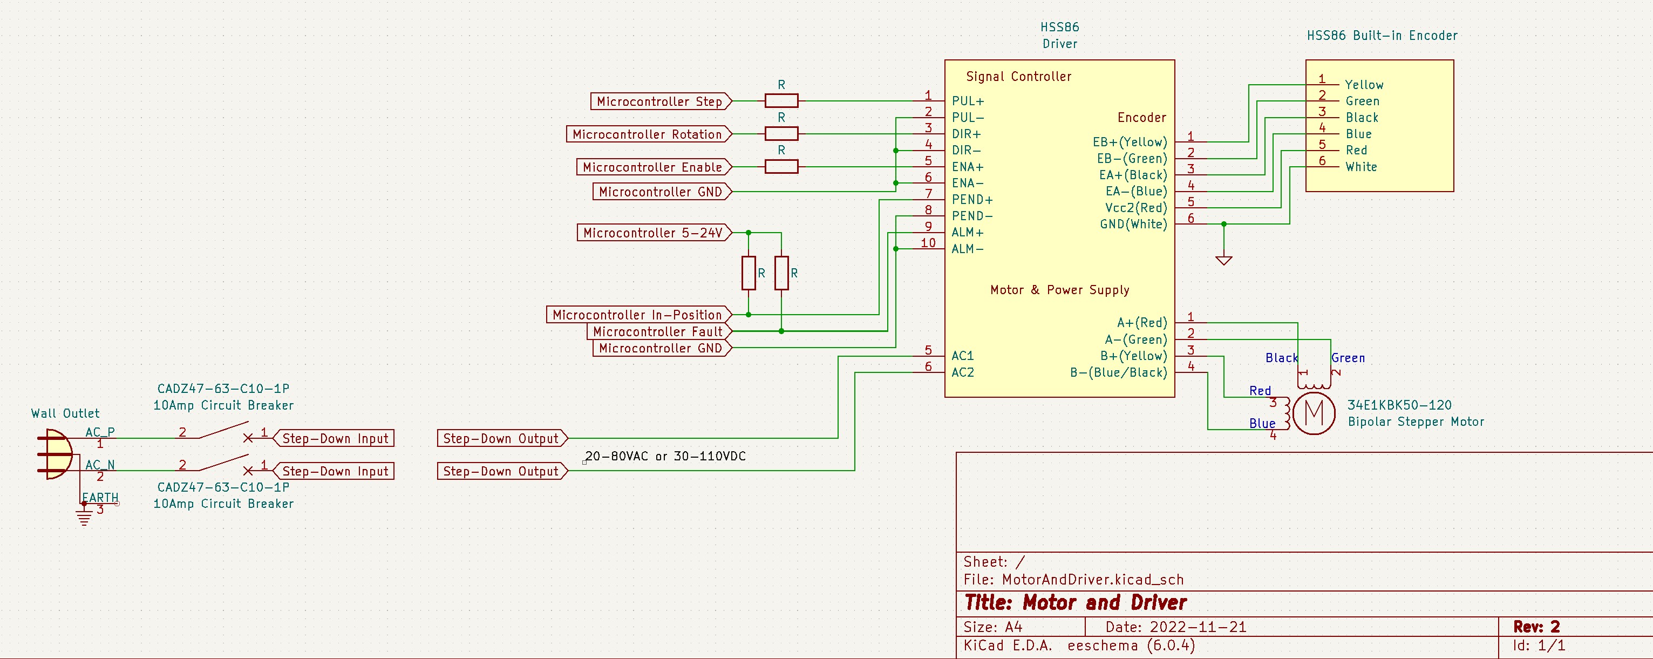
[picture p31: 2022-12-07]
Documentation/Images/Schematics/DriverAndMotorRevisionTwo.jpg

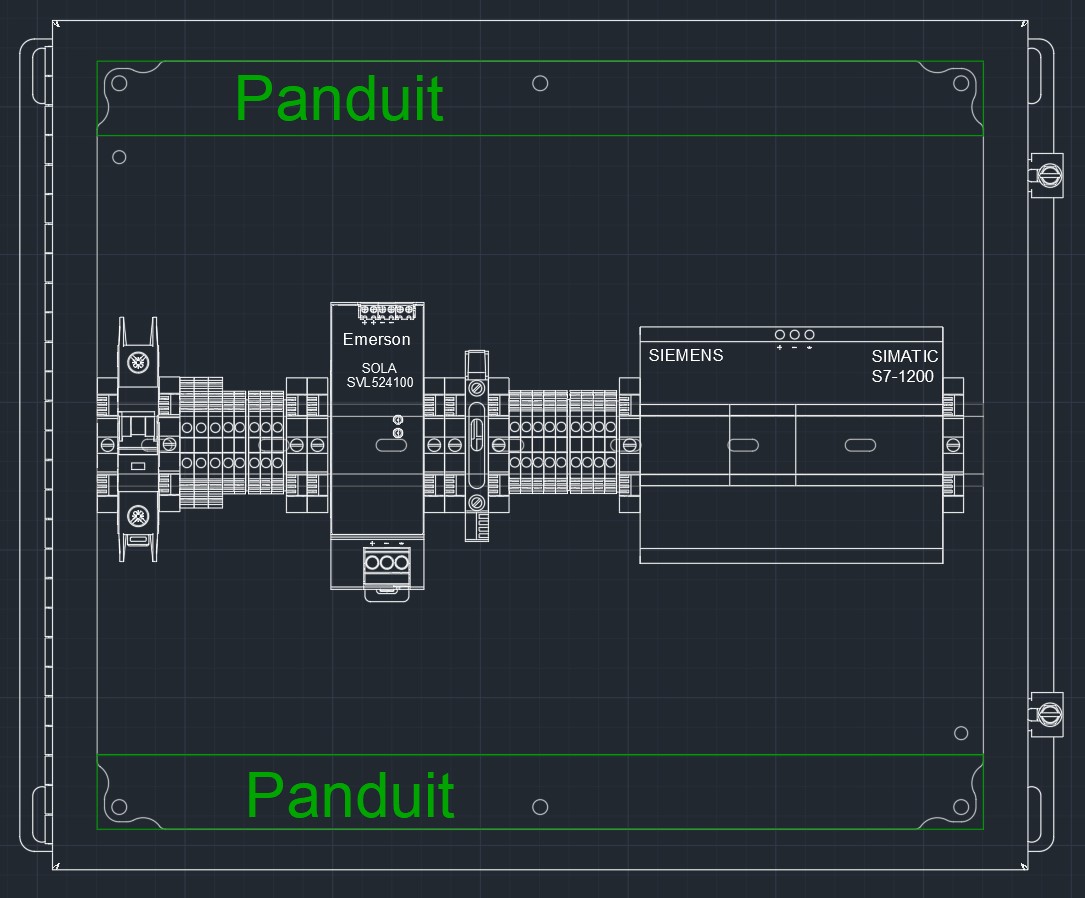
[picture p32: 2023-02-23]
Documentation/Images/Schematics/Dinrail_Layout.jpg

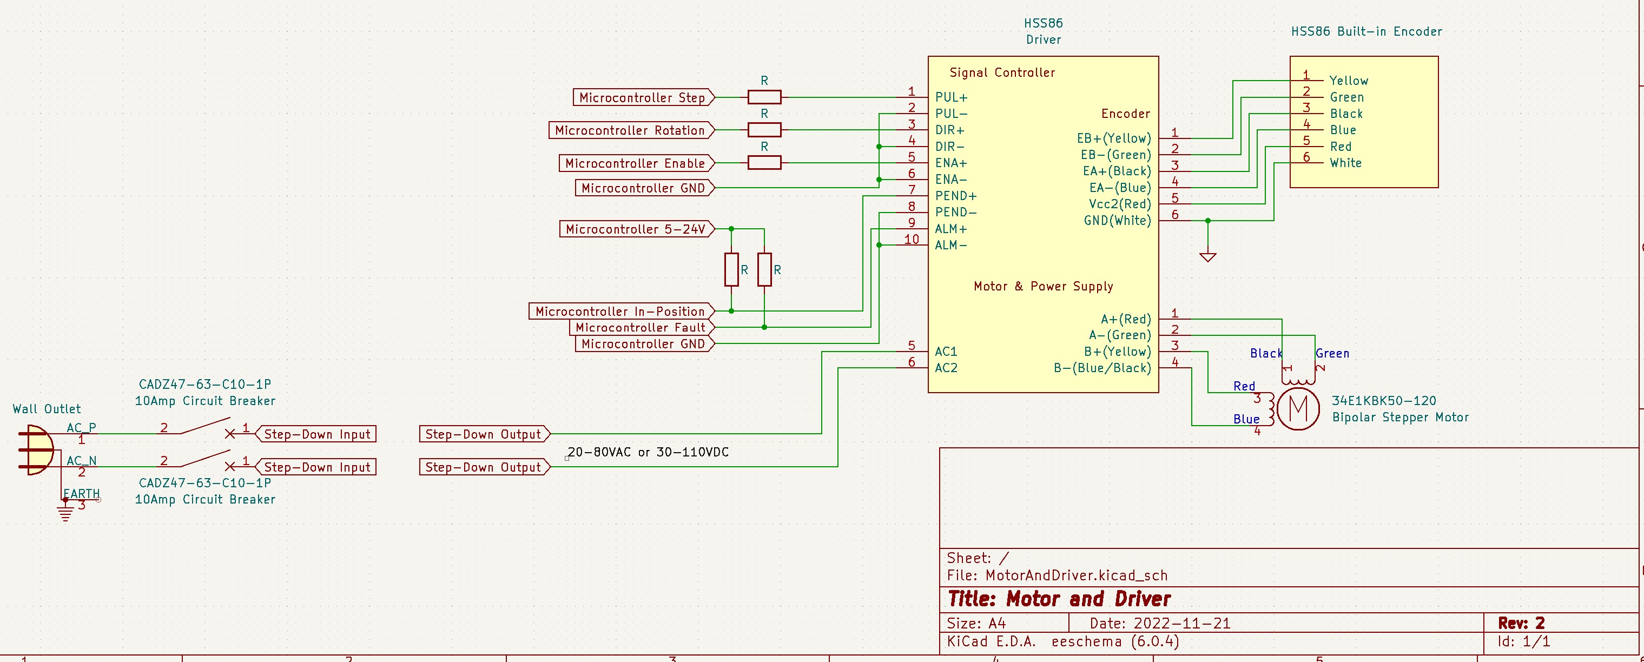
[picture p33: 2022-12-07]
Documentation/Images/Schematics/DriverAndMotorRevision.jpg

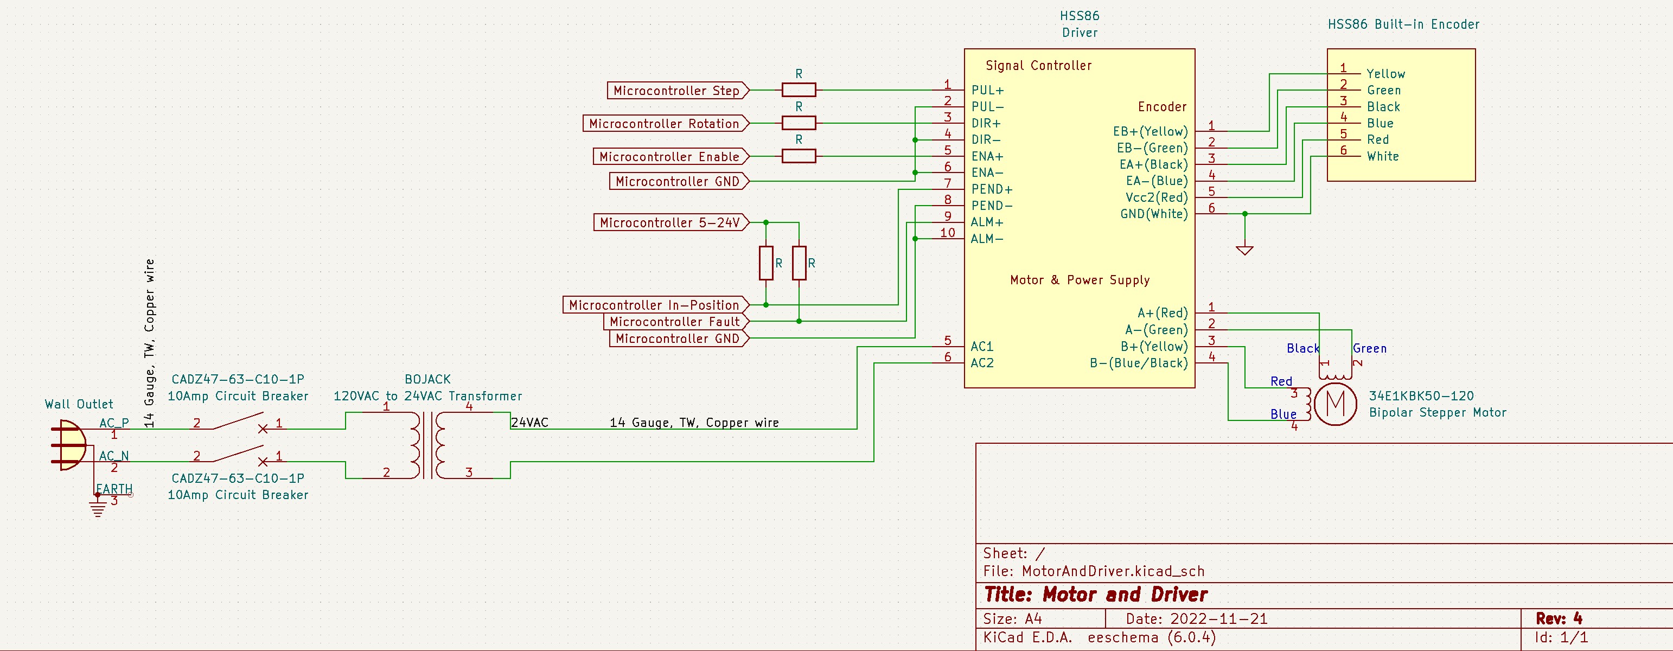
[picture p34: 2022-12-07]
Documentation/Images/Schematics/DriverAndMotorRevisionFour.jpg

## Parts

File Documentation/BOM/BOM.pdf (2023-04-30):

Quantity | Item | | Cost
1 | Stepper Motor | $ 284.00
1 | Motor Driver | $ 213.00
2 | 4 A Breaker | $ 60.00
2 | USB Voltmeter | $ 45.98
2 | Barcode Scanner | $ 79.98
1 | RFID Reader | $ 14.99
1 | Linux PC | Provided
1 | USB NIC | $ 15.99
1 | Siemens Memory | $ 90.96
1 pack | LEDS | $ | 5.95
1 | Siemens PLC | Provided
3 | Solenoid Locks | $ 37.47
2 | Sensors | Provided
1 | Enclosure | Provided
Total | $ 848.32

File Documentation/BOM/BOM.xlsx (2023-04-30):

Subsystem | BOM Costs (In Order) | Total
Motor
 | Stepper Motor | $284.00
 | Motor Driver | $213.00
May not need | 10A Breaker |  | $17.98
 | 2kOhm Resistors | $5.73
May not need | 4A Breaker |  | $30.00 | Quantity | Item | Cost
Identification |  |  |  | 1 | Stepper Motor | $284.00
 | Voltmeter |  | $45.98 | 1 | Motor Driver | $213.00
 | 1D/2D Code Scanner | $79.98 |  | 2 | 4 A Breaker | $60.00
 | RFID Reader | $14.99 |  | 2 | USB Voltmeter | $45.98
Gifted | ThinkCentre PC |  | ??? | 2 | Barcode Scanner | $79.98
 | USB NIC | $15.99 |  | 1 | RFID Reader | $14.99
 | Siemens Memory | $90.96 |  | 1 | Linux PC | Provided
 |  |  |  | 1 | USB NIC | $15.99
PLC |  |  |  | 1 | Siemens Memory | $90.96
 | 24V LEDs | $5.95 |  | 1 pack | LEDS | $5.95
Gifted | PLC |  | $300 - $500 | 1 | Siemens PLC | Provided
 |  |  |  | 3 | Solenoid Locks | $37.47
Security Locks |  |  |  | 2 | Sensors | Provided
 | Solenoid Locks | $37.47 |  | 1 | Enclosure | Provided
Gifted | Inductive Sensor
 | Door Hinges | $27.99 |  |  | Total | $848.32
 | Pilot Dash Light | $17.85
Sensors
 | Diffuse Sensors |  | $327.00
 | Female Cord Set | $34.50
User Interface
 | LCD |  | $269.99
 | Nexus Stand |  | $89.95
 | Total Costs so far: | $828.41
Safety
 | Terminal Block Relays | $23.92
 | Switches | $465.03
Power
 | All
 | New Total: | $1317.36

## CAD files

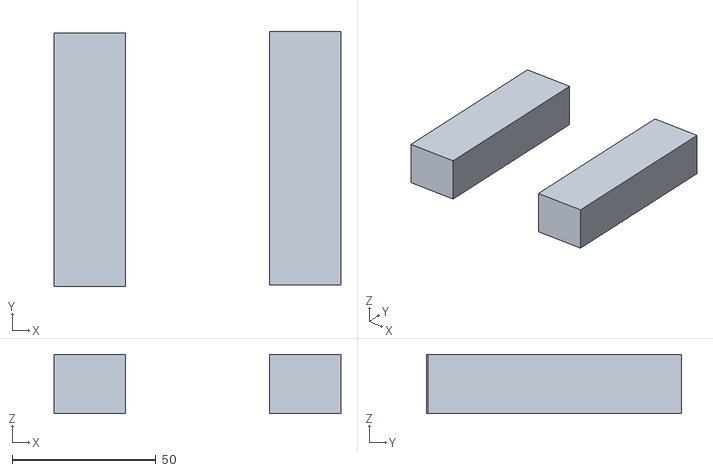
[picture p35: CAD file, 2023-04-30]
Documentation/3D Models/Door Components/STL Files/door assembly - Safety_Sense-1.STL
99.8 x 88.6 x 20.6

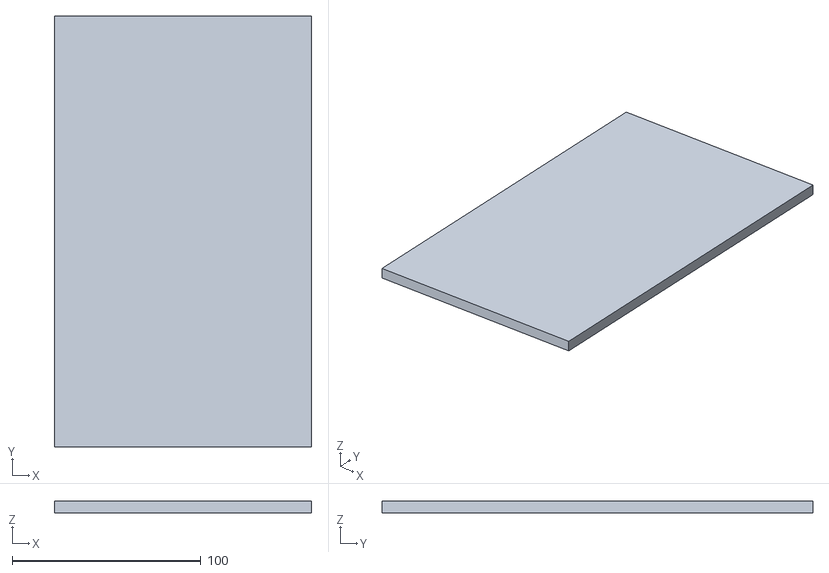
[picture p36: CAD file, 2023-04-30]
Documentation/3D Models/Door Components/STL Files/door assembly - Door-1.STL
136.5 x 228.6 x 6.35

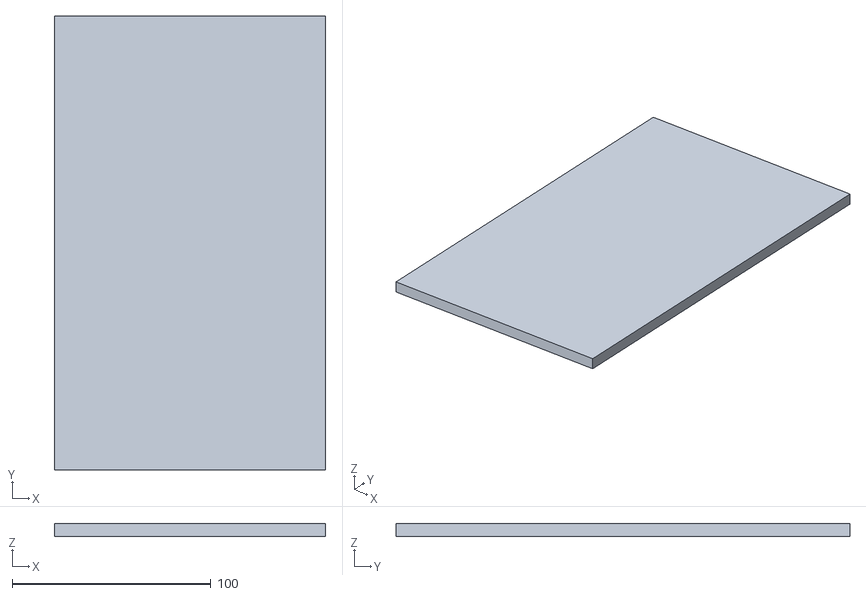
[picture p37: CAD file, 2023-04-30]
Documentation/3D Models/Vending Machine Frame/STL Files/Vending Machine Frame - door assembly-3 Door-1.STL
136.5 x 228.6 x 6.35

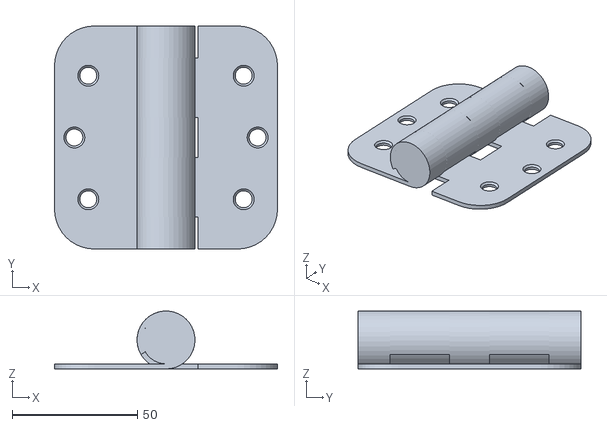
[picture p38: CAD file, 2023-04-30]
Documentation/3D Models/Door Components/STL Files/door assembly - 1798A21_Surface-Mount_Hinge_with_Holes-2.STL
88.9 x 88.9 x 23.1

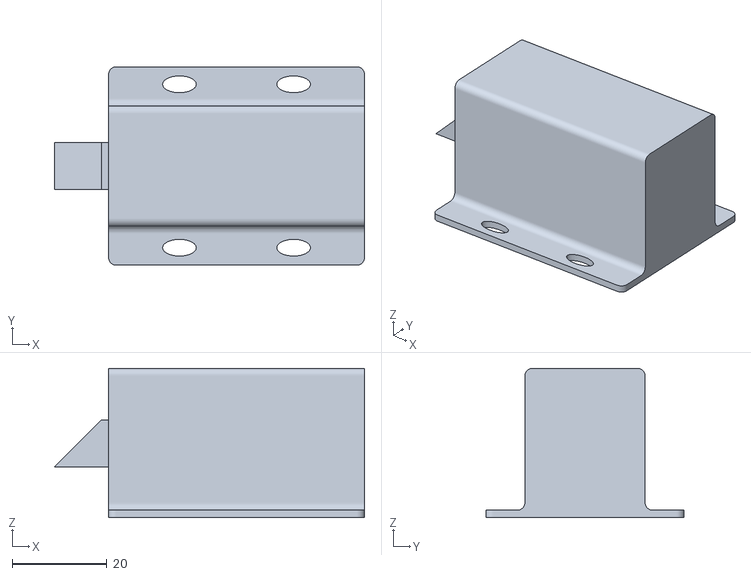
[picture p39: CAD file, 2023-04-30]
Documentation/3D Models/Door Components/STL Files/door assembly - Solenoid Lock-2.STL
65.5 x 41.9 x 31.6

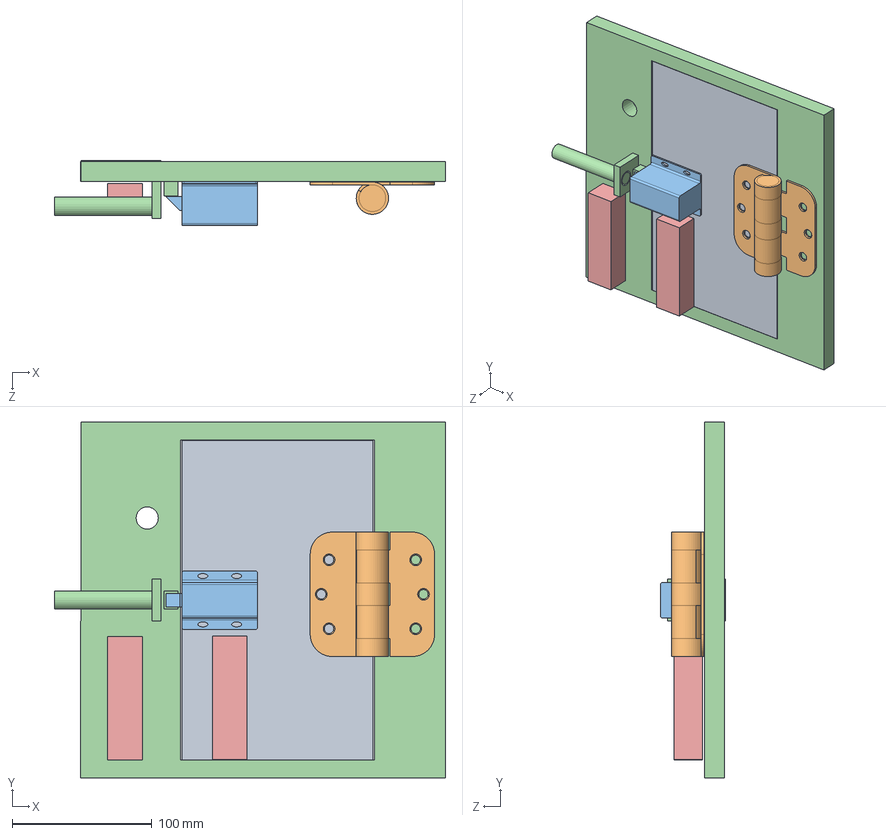
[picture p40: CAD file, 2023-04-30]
Documentation/3D Models/Door Components/SolidWork Files/door assembly.SLDASM
279.4 x 254.3 x 46.7 mm
Door
1798A21_Surface-Mount_Hinge_with_Holes
Solenoid Lock
Door Frame
Safety_Sense

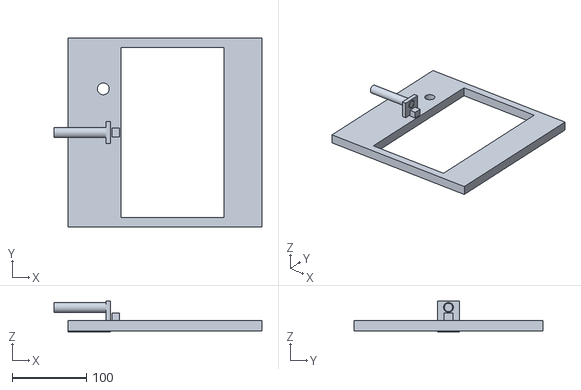
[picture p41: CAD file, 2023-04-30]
Documentation/3D Models/Door Components/STL Files/door assembly - Door Frame-1.STL
279.4 x 254.3 x 41.4

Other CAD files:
Documentation/3D Models/Vending Machine Frame/STL Files/Vending Machine Frame - door assembly-3 Solenoid Lock-2.STL
Documentation/3D Models/Vending Machine Frame/STL Files/Vending Machine Frame - door assembly-1 Safety_Sense-1.STL
Documentation/3D Models/Vending Machine Frame/STL Files/Vending Machine Frame - door assembly-3 Safety_Sense-1.STL
Documentation/3D Models/Vending Machine Frame/STL Files/Vending Machine Frame - door assembly-2 Solenoid Lock-2.STL
Documentation/3D Models/Vending Machine Frame/STL Files/Vending Machine Frame - door assembly-1 1798A21_Surface-Mount_Hinge_with_Holes-2.STL
Documentation/3D Models/Vending Machine Frame/STL Files/Vending Machine Frame - door assembly-2 Door-1.STL
Documentation/3D Models/Vending Machine Frame/STL Files/Vending Machine Frame - door assembly-2 1798A21_Surface-Mount_Hinge_with_Holes-2.STL
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

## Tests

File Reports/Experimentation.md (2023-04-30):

# Experimental Analysis  
 
## Identification Subsystem 

### Purpose of the subsystem  
---
The purpose of the subsystem is to store student information into a database and automatically assign the student the correct board depending on class selection. The system has not met all of the original constraints due to issues obtaining the part orders. It is important to note that the original specifications have been met in another way.  

The customer required the program to do a few things: store the student ID, name, email, class, and term, before ordering the machine to bring the appropriate device to the door.  

Most of the constraints enumerated in the signoff have not been met due to parts never arriving for the team, however, the constraints have been partially satisfied by substituting the needed hardware with software. Any other constraints where parts were not received and not able to be programmed are considered out of the scope of this project.  

---
### Constraints/Specifications
---
Below is a list of the constraints for the ID system. They are numbered C1 to C9

C1: Barcode Scanners shall be low power and consume no greater than 5 V 0.5 A.  

C2: Barcode Scanners shall be able to decode Code-128 barcodes  

C3: Barcodes shall be of decent quality to follow ISO 15416 standard. Assures that the codes can be read by any scanner  

C4: RFID Card Scanner shall be low power and consume no greater than 5 V 0.5 A

C5: RFID Card Scanner shall operate on 13.56 MHz commonly used for higher security access badges, like the school Eagle Cards  

C6: A Barcode Scanner and Card Reader will be monitered by USB voltmeter to ensure correct operation  

C7: The PC shall run on Windows 10 to provide the needed applications for PLC and Database  

C8: The PC will provide an ethernet port to communicate with the PLC through a USB NIC (network interface card)  

C9: The PC will provide at minimum an Intel Core i5-8400H or stronger CPU and 16GB RAM to support PLC programs  

Constraints C1-C3 required a barcode scanner that could scan the boxes and use a required rating of 5V, 0.5A. Since the scanner was never received by the team, the application now allows the customer to enter codes manually through the GUI application. The program still automatically assigns the board as originally required. 

Constraints C4-C6 required the RFID scanner to read data off the school ID card and automatically fill the database with the student ID. Since the scanner was never received, the program now has the student enter his/her own ID and error checking the entered information and the Voltmeter is no longer required without the 2 scanners. 

Constraints C7-C9 required the team to have a decently rated Windows 10 computer for running the PLC, GUI, and database, but due to IT policies, the computer was not allowed to be purchased by the school. Instead, the school provided a Linux PC for the team to use for programming. The PLC application was used from the school lab due to never receiving the memory card for our acquired PLC. 

---
### Experimental Procedure  
---
To test this subsystem, a user entered data through the GUI and it was verified to be inside of the database on the host with the correct assigned board. The inventory entered in the program was also verified to be inside the database. The running of the motor will be demonstrated in the PLC analysis, and the Error checking will be shown in the GUI analysis. The communication via OPC was verified as shown in the below video by sending and receiving signals to and from the tag. 

---
### Expected Results  
---
The team expected the student data to be in the database in alphabetical order along with the rented board determined by the step count handled by the program. The inventory was also expected to be present with its rented and stored date because a student cannot rent without a device in the machine.
A total of 10 random students were entered into the database along with 15 random devices. We also expected the motor to turn correctly based on the values sent to the PLC. 

---
### Collected Data
---
Constraint C1 is unable to be met in the original way to do unforseen ordering circumstances. Instead, the team has allowed the manual entry of boxnumbers through the GUI system. The results can be shown in the third figure below where the numbers are inside of the database after entry.  

Constraint C2 has been deemed out of scope by the team due to never receiving the barcode scanner as mentioned for C1.  

For Constraint C3, barcodes were never made since the barcode scanner was not received. The devices can instead be entered by the boxnumber written on the device.  

Constraint C4 is unable to be met in the original way to do unforseen ordering circumstances. Instead, the team has allowed the manual entry of Student ID numbers through the GUI system. The results can be shown in the second figure below where the IDs are inside of the database after entry.  

Constraint C5 has been deemed out of scope by the team due to never receiving the Card reader as mentioned for C4.  

The USB Voltmeter was never received and therefore C6 cannot be tested. 

Constraint C7 is not met due to ordering restrictions with the IT department. Instead, a Linux PC with the appropriate specifications was provided by the college.  

Constraint C8 has been deemed out of scope due to never receiving the USB NIC from the placed order forms. 

For testing C9, the team went into the specifications of the PC provided by the college to verify that the CPU and Memory. 

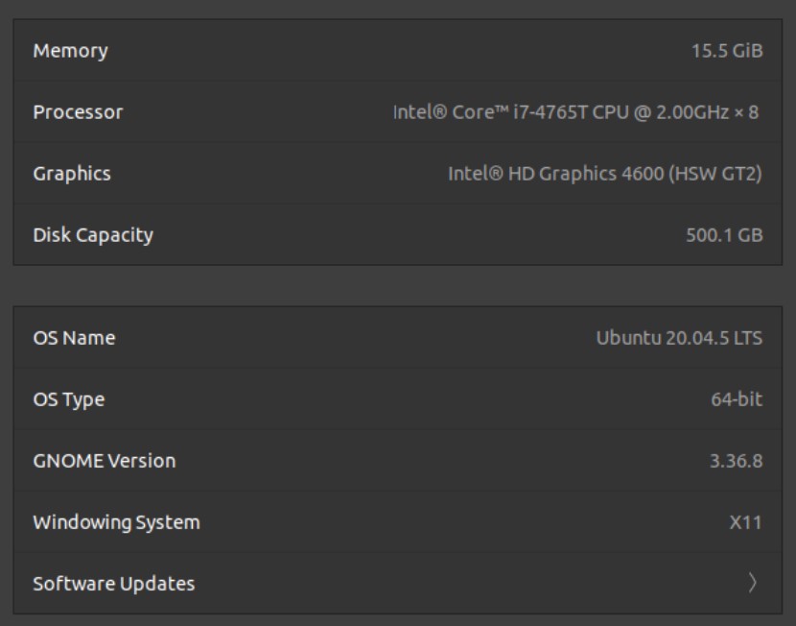
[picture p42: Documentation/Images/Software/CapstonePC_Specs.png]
SpecsPC
  

As you can see in the photo above, the CPU is stronger than an Intel Core i5 and the Memory is 16 GB.

Below you can see the results of running the database program while taking input from the GUI. The database needed to hold all 10 test entries in the student database and keep track of the rented device and student information. 

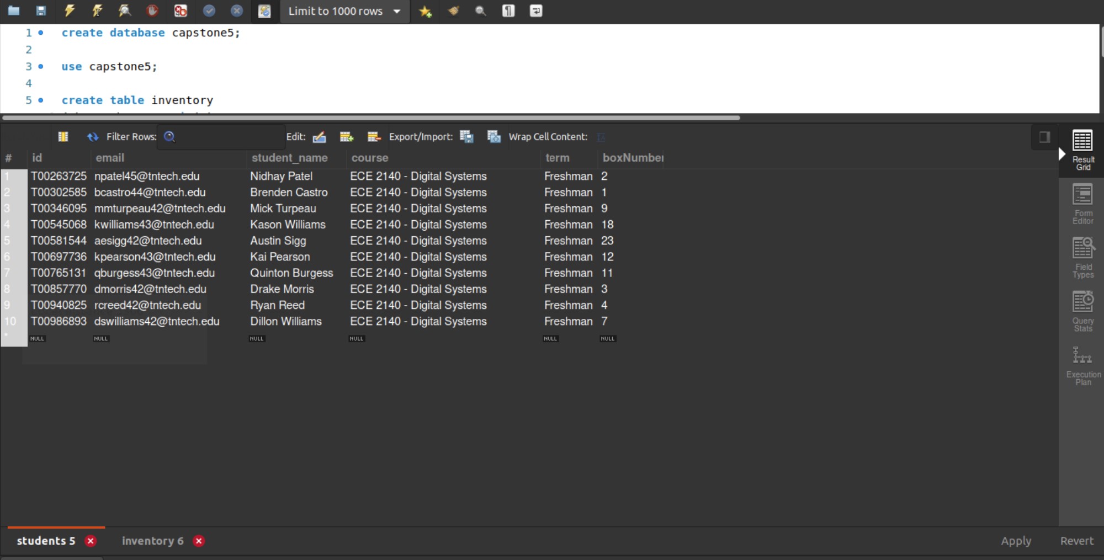
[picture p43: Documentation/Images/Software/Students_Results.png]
Students_Results
  

Below you can see the results of the inventory table after testing the entry of 15 devices and the renting of 10. The devices should be removed in order of entry into the machine.  

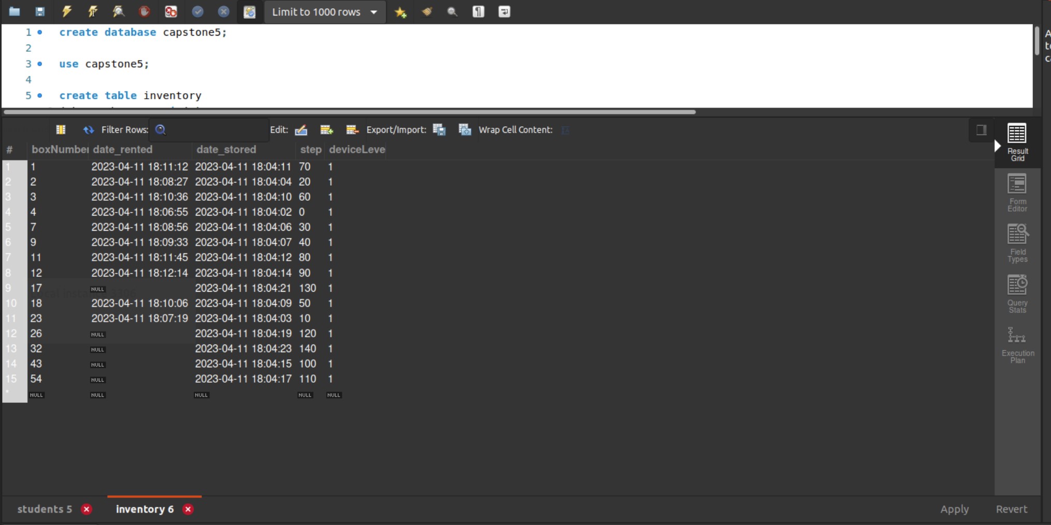
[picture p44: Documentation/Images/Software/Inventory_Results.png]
Inventory_Results


---
### Data Interpretation
---
For C1, you can see in the third figure that the boxnumbers were correctly taken in by the database along with the rented and stored dates. This is the result the team expected to see when entering through the database.  

Constraint C4 is satisfied by allowing the user to enter his or her ID into the GUI. As you can see the data entered in figure 2 is all present in the database as expected.  

Given that the PC has a Core i7 and 16GB of RAM, the comupter specs are decent enough to run the PLC application needed for programming. This satisfies constraint C7 and C9 in the list.   

In figure 2, the student data was entered and stored in the correct format. All required information from our customer is provided through the GUI and stored after error checking procedures.  

In figure 3, the device information was stored correctly after being entered by an administrator. Students are not allowed to decide the board received and therefore the device location is also stored in the database. 

---
### Measures of Success
---
The measure of success for the ID system states that the program must correctly store the boxnumbers and student information. For the OPC communication, the program needed to send and receive signals to and from the database. In the following video it can be shown that the OPC communication correctly activated the motor, and the previous results show the data from the GUI being stored correctly into MySQL. 

Video : https://youtu.be/tVvsogPO3sM

---
### Future Improvements
---
Several improvements can be made on this system because parts need to be installed in a future version, and the database can be expanded. The next team that receives the project must make sure to install the barcode scanner and card reader to the machine. The card reader is needed because, as of now, the student can enter any correctly formatted T#. The system should take information from the card so a student cannot fake information. The voltmeter must also be acquired to monitor the operation of the barcode and card scanners.  

## GUI Subsystem

### Purpose of the subsystem
---
The purpose of the graphic user insterface is to take information from the user and store it into the database through the ID subsystem. The interface allows for a convenient way to rent a device for a class and provides error checking to verify information is in the correct format.

The interface is able to let a user input information into the ID subsystem and provide the student with notifications while renting a device. The GUI must follow certain constraints determined during the design of the project. The team was not able to order a touchscreen for the project, but received a ubuntu 20.04 computer from the school IT department instead. 

---
### Constraints/Specifications
---

  1. UI must run Windows/Linux environment to run the application.
  2. Must have HDMI or type C or USB port to connect to PC.
  3. UI must be at least 15.6" (diagonal) because of the TIA (Totally Integrated Automation) Portal application.
  4. UI must be anchored to prevent theft problems.

Constraints C1-C3 are satisfied by the computer provided to the team by the IT department. 

Constraint C4 was satisfied by a personal laptop of a team member, where he programmed a custom PLC ladder logic program. 

Constraint C5 will need to be improved upon in the next rendition of the design by a future capstone team. Due to a lack of parts, the machine will not be moved into the Brown student lounge, so an anchored PC was not needed. 

---
### Experimental Procedure
---
To test this subsystem, a user entered incorrect data and correct data into the UI to verify the operation of error checking. The UI will provide popups whenever it detects and error, and will not take any data until the error is resolved. The data will be checked to make sure incorrect data was not entered into the database. There is operations in the code to prevent SQL injection into the database, which will be verified by trying to inject through the GUI input box. There is a command that will shut down the program as well and will be tested after data is entered. 

---
### Expected Results
---
The team expected to see all errors popup during the correct time and allow data storage when the GUI was not faced with an error. The GUI was also expected to prevent incorrect data from being stored during an error and prevent injection through the input box located on the screen. Every error was checked by first entering correct data, then inputting incorrect data to the ID system through the GUI. The team also attempted to inject a query through each input box twice in case a first attempt catches an error. 

---
### Collected Data
---

Below is the all the data that was collected for input validation for different fields if a student were to mistype some of the input fields or if they were to skip some fields and hit the submit button directly.

| | | 
|:---:|:---:|
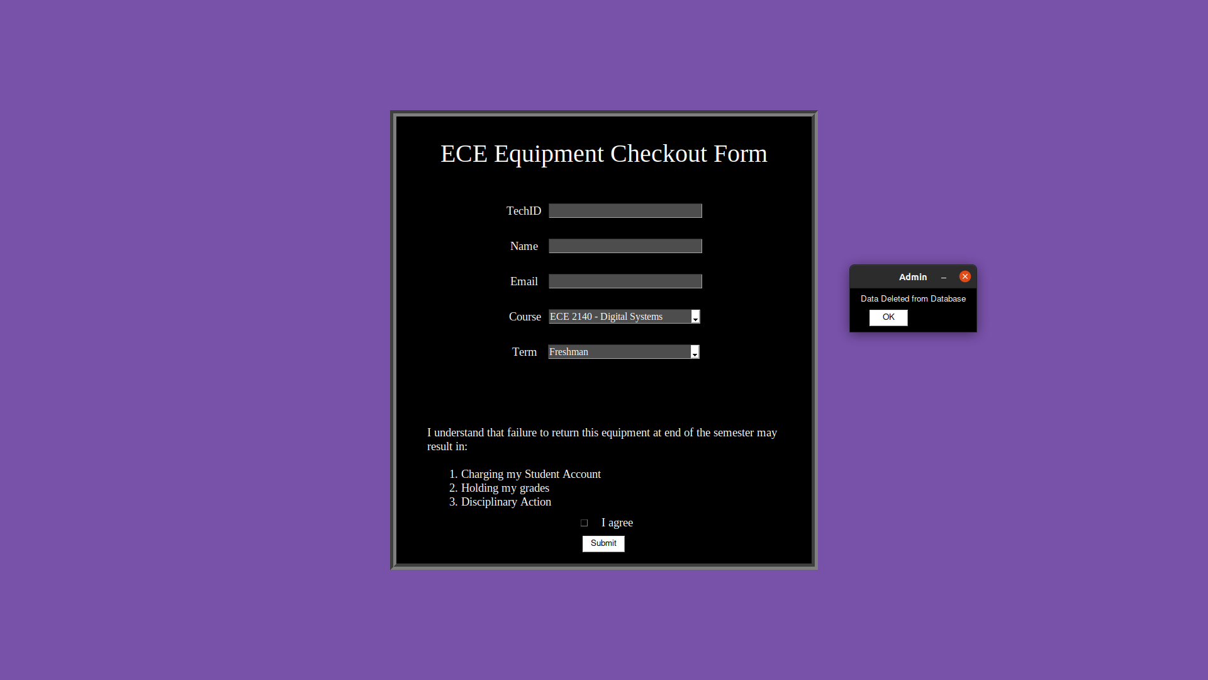
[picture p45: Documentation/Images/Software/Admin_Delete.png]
Delete
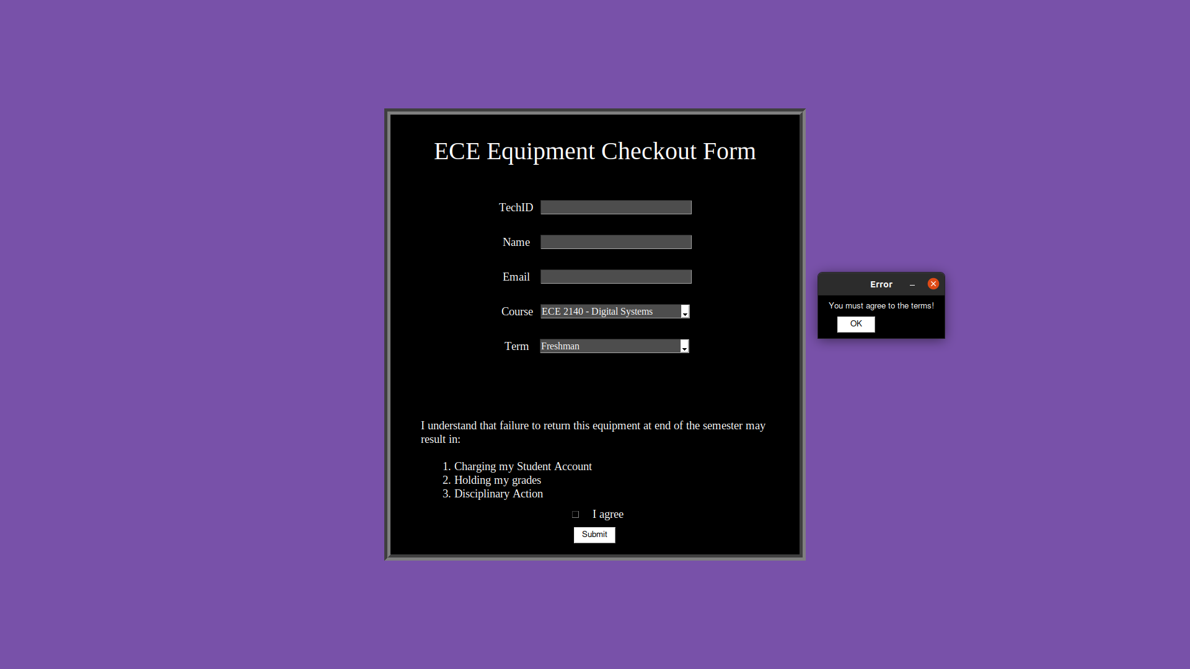
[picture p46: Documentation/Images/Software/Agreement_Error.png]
Agree
 Figure 1: Admin_Delete|  Figure 2: Agreement_Error| 
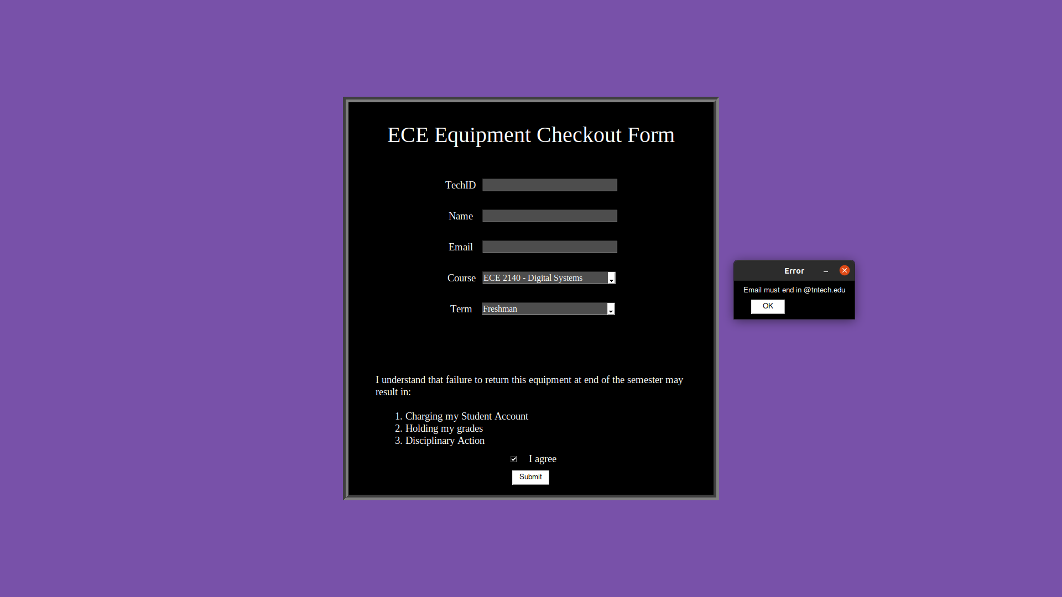
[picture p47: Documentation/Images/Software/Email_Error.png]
Email
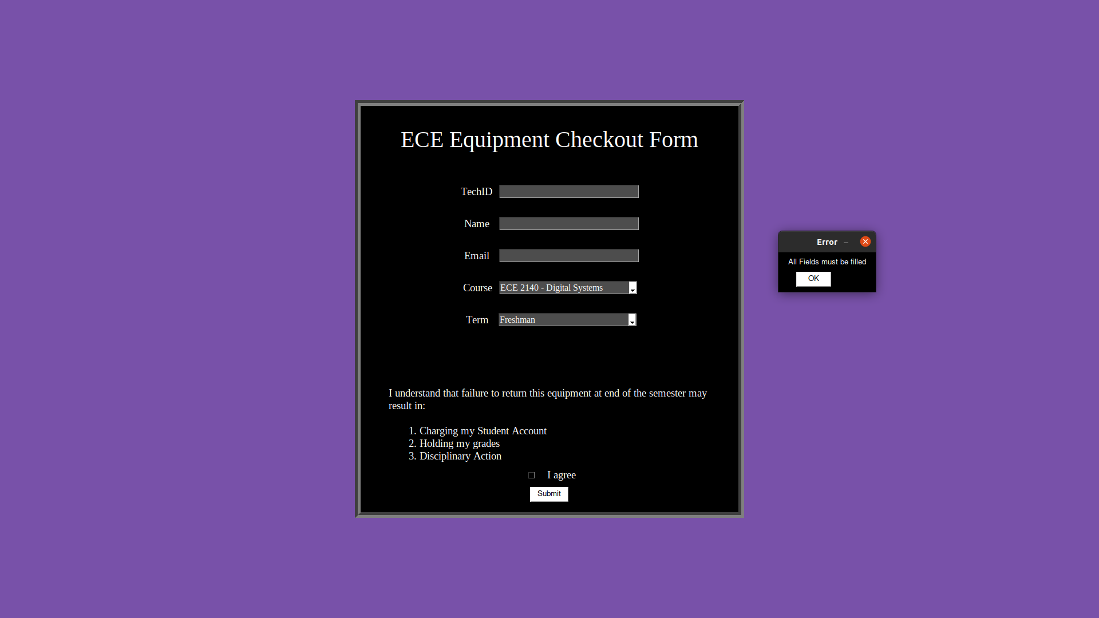
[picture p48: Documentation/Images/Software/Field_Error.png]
Field
 Figure 3: Email_Error|  Figure 4: Field_Error|
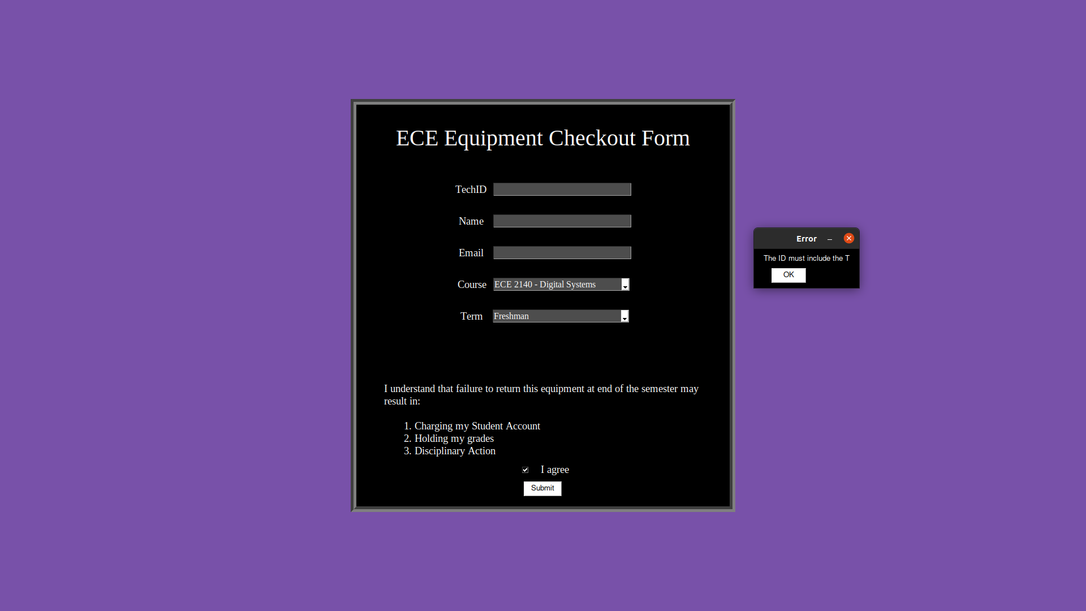
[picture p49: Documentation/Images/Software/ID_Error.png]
ID_Error
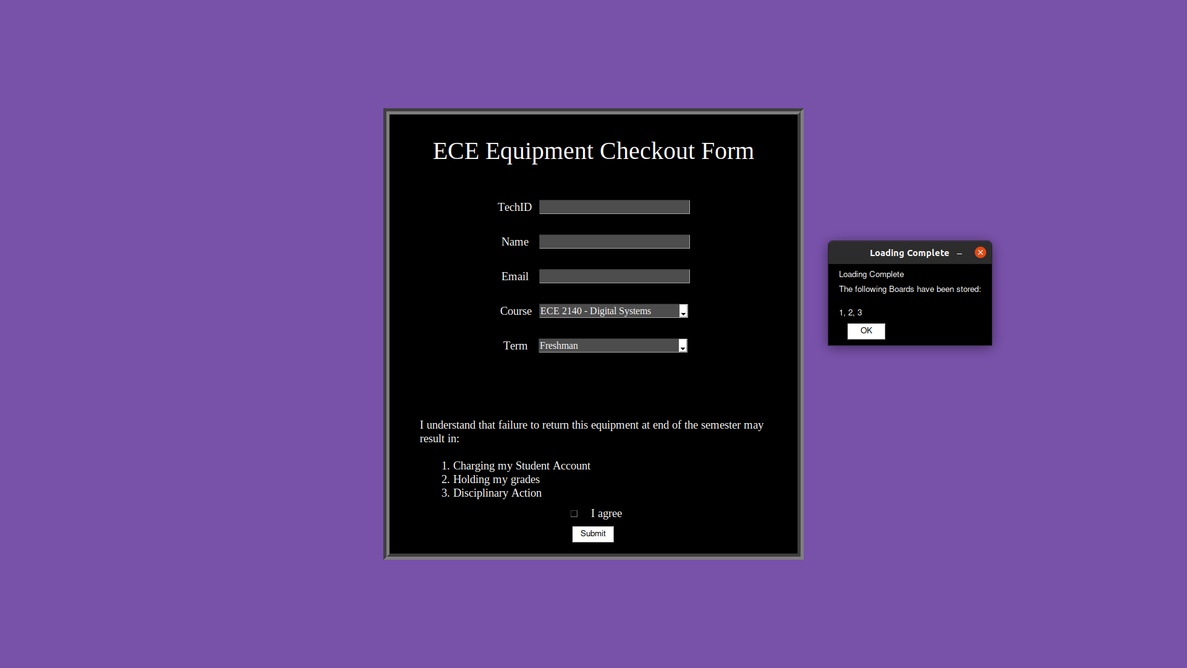
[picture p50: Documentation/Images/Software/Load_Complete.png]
Load_Complete
 Figure 5: ID_Error|  Figure 6: Load_Complete| 
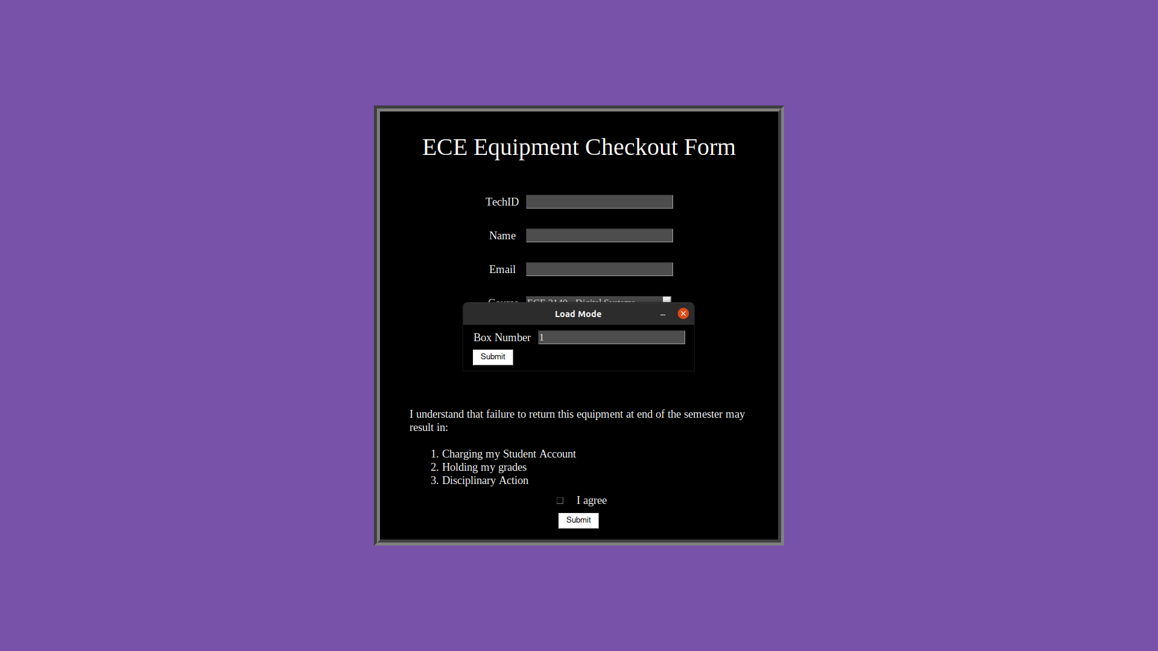
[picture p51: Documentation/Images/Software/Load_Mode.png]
Load_Mode
 Figure 7: Load_Mode| Name_Error Figure 8: Name_Error| 

---
### Data Interpretation
---

For C2, we can clearly see that the computer provided by IT departmnent was able to run the GUI written using python in Linux Environment. Also, we can see that different errors were generated for different input fields in the pictures listed above.

If needed to delete the database by an associate then the command that is set to do so is "delete" in ID field and "admin" in name field. This keywords can be changed anytime as per the needs of associate, and if did so correctly then the figure 1 depicts what it would return and will delete the information stored in database.

For the load mode, the keyword to enter the number of boards is "load" in ID field and "admin" in name field. If did correctly, it would open a prompt where an associate would type in the boards manually. This was done as a substitute because of the barrring ordering issues and parts not arriving on time. The boards loaded propertly in the database can be seen in ID subsystem (figure 3).

For different input fields, different errors can be seen as shown in table above.If a student were to input the email address incorrectly, then the popup shown in figure 3 would let the student know that they are typing the email wrong. If the name entered by the student in the name field doesn't have first and last name then the program would throw an error to them saying they need to type the first and last name as shown in figure 8. If for some reason, a student forgot to type the T in the ID field then the program would tell the user that they need to enter "T" before the ID as seen in figure 5. If a student were to skip one of the input fields and agree to the terms and conditions and try to submit the information then figure 4 shows that it would throw an error message asking the user to fill all input fields.

At last, if the student filled all the information, but failed to agree to the terms and conditions and tried to submit the information then the program wouldn't let it do so and ask the user to select and go over it as shown in figure 2. All these validations are also protected against SQL injection as each entry field is looking for specific keyword. For example, ID has to start with "T", name field is looking for only two words i.e. First and Last Name, for email the entered username has to end with Techs domain of tntech.edu, and at last the drop down menus are read only so the students don't have any way to inject queries and extract information of students.

To protect students from accidentally closing the program we implemented a special keybinding so that students don't close it intentionally or unintentionally and access the student information. To do so, the program is set to close with the keybinding of "Alt + Z" as our team thinks that this combination wouldn't be used that frequently.This keybinding can be changed like other commands by associates if needed.

---
### Measures of Success
---
The measure of success for the GUI system states that the program must be easy to use and also must prevent SQL injection by throwing errors when inforamtion is incorrectly entered. The following video shows the layout of the GUI which is also shown above, and the video also shows errors being thrown when information was incorrectly entered. 

Video : https://youtu.be/tVvsogPO3sM

---
### Future Improvements
---
Several improvements can be done to this subsystem. In future, if the IT department allows to order the Touchscreen UI as originally proposed then that can be used for GUI as that would get rid off extra hardware. Also, another improvement would be making the GUI more intuitive so students or associates could navigate it easily, also  if the future capstone team were to get SD card for PLC then they could integrate the PLC with the program so that they both can perform synchronously, and at last the machine is made up to hold one board but in case if they students were to expand the design so that the machine can hold multiple boards then some modifications would have to be done for GUI with some additonal details.

## PLC System

### Purpose of the Subsystem
---
The purpose of the PLC system is to be the middle-man between our database and our physical peripherals such as the motor and LEDs. The reason we chose to use a PLC in addition to a Linux PC is because PLCs are designed to handle physical control faster and more efficiently than a PC.

---
### Experimental Procedure
---
To test this subsystem, we connected the only peripheral we have available to us, the motor driver, and aliased its inputs (STEP, DIR) with tags in the PLC. When these tags are energized and unenergized, the motor should be able to step and change direction based on the state of their respective tags. Because most of the constraints revolving around the PLC are about its peripherals, there are not many constraints that can be experimented on in this section.

---
### Expected Results
---
If everything is connected properly, and the OPC client can ping to the PLC, the OPC should be able to change the state of a tag and read its state. The PLC should also be able to revert the state of the tag changed by the OPC for the next run.

---
### Collected Data
---
Constraints C1 and C2 required us to have the memory card for our PLC, which does satisfy these constraints. But, due to ordering issues, we are using the PLCs in our PLC lab, which have 8 digital input and outputs. So, with what we have, C1 is satisfied. However Constraint C2 is no longer within the scope of this project due to us swtiching to a PLC with 8 digital inputs and outputs.

Constraint C3 is satisfied, even with the ordering issues. The PLC setup that we are using is 24-inches long, and less than 6-inches deep and tall. So, our system will fit within a 3x1x1 foot area, and C3 is satisfied.

Constaint C4 is satisfied with the PLC we are using. The PLCs in the lab have two 48V fuses, one that is rated for 2A and the other for 4A. This satisfies IEC-61131-2(6.4.4.3) for protection from physical damage.

Constraint C5 is satisfied by the use of a custom OPC client that can read-from and write-to the PLC.

https://user-images.githubusercontent.com/100802994/231836664-d108fc11-3d49-4a41-928a-dcc6a42da2b6.mov

Above is a video recording of us using the OPC client to control the PLC, which is controlling the motor driver.

OPC

The image above is of the OPC client running on our Linux VM. The client first reads the value of the controller tag, then changes it to "true" or "energized" and reads it again. This along with the video show that the OPC is able to communicate with the PLC.  

---
## Data Interpretation
---
The video collected above shows how constraint C5 was satisfied through our OPC client. When the client is ran, it energizes a controller tag associated with stepping the motor. As will be shown (as best as we can) in the motor system analysis section, we did not touch the PLC code in our Studio 5000 software. Instead we had a stopwatch up on the screen to time how long it took the motor to complete a full rotation.

---
### Measures of Success
---
The measure of success for the PLC system states that the program must correctly control the peripherals given signals from the OPC. In the following video, it can be seen that the motor correctly activates and turns after being given the signal from the OPC. The other peripherals have not been connected because the parts were never received. 

Video : https://youtu.be/Vv9zIDt42ac

---
### Further Improvements
---
The main point that can be said about future improvements is ordering the peripherals and writing the code to control them. Another improvement that could be made is to the pulsing sequence for stepping. Currently it is two TON timers that read the .DN boolean of the other timer. There is a way to make a rising-edge detection sequence using only one timer, but I do not rememeber how. If this was implemented, the code would look cleaner and allow for more efficient pulse width modulation.

## Safety System

### Purpose of the Subsystem
---
The sole purpose of this system is to secure the safety of the users and the internal components of the device. The primary functions of the system come from the consumer's cabinet restrictions. Using non-contact Inductance Proximity sensors, both the consumers and inner contents of the machine shall have an extra shield from possible harm. This shall also prevent any potential damage and interference in the system’s operations.

In contrary of the original design using “RFID Coded Safety Sensors”, for budgetary reasons it was substituted for a closed loop Proximity Sensor system. As shown below, the safety system functions outside of the normal operation cycle of the machine. This allows the machine to have a “double check” in the case of tampering with one of the lock sensors. This also overrules if there are any issues with the PLC. Both the Security System sensors and Safety System sensors are required to continue operation of the device.



Constraint C1 has been fulfilled by the general functionality of the proximity sensors. Since there are no doors to be sensed, the sensors have been thoroughly tested with other metallic objects.

Constraint C2 has been resolved by using a closed loop system as shown above. If this project is carried over to another team, the original system design using RDIF Safety Sensors is still viable.

Constraint C3 has been fulfilled by using relays to control the enable state of the motor driver.

---
### Constraints/Specifications
---

The design constrants are as followed:

**• The relay shall be aware of the state of each cabinet door all times. (C1)**

**• The system shall be redundant and separate from the normal operations of the PLC. (C2)**

**• The system must overrule all other functions of the system. The motor shall not have any motion while there is an error in place. (C3)**

Constraint C1 has been fulfilled by the general functionality of the proximity sensors. Since there are no doors to be sensed, the sensors have been thoroughly tested with other metallic objects.

Constraint C2 has been resolved by using a closed loop system as shown above. If this project is carried over to another team, the original system design using RDIF Safety Sensors is still viable.

Constraint C3 has been fulfilled by using relays to control the enable state of the motor driver.

---
### Experimental Procedure
---

To properly test this system, the sensors and relay system was wired and tested using in-lab power supply and DMM. The sensors were originally tested on aluminum material, and has since been experimented with other ferrous material as listed on the datasheet. After wiring the sensors and relay to match the required logic. The logic prepared resembles that of a simple AND gate, meaning all of the sensors must be activated for a signal to be sent to the motor driver. When the enable recieves a positive input, the motor stops all movement.

---
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

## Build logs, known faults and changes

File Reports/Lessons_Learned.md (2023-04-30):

## Lesson Learned Team 5

## Austin Sigg
1. Everyone had sufficient techinical knowledge or means to learn said knowledge required to sufficiently perform all design tasks in our Capstone project.  Organizationally we could have had a more solidified structure in the roles each of us had, like not having a designated hierarchy with a 'team captain' sometimes resulted in confusion on who's responsibility it was to do what.  Overall though the functionaility of our team through out this project did end up working well besides a few minor things not even worth mentioning.
2. The largest problems all came mostly from misunderstanding on what exactly was wanted in reports. A lot of time could have been saved for everyone if we more easily grasped and comprehended what information our signoffs, reports, and experiments should specifically be composed of.  One problem we did not expect was that our parts may not arrive on time or at all. 
3. I would have gotten ahead on signoffs far quicker so as to have ordered parts sooner. I would have written my signoffs to compose exatly what my supervisor wanted from them so as to waste less time. 
4. Its best for everyone to have their own tasks and responsibilities in the team, but at the same time for everyone to work on everything together so as to have as many minds as possible working on all parts of the project giving each their own perspectives and skills to be utilized.
5. Get ahead and don't get behind; if you get behind on your work then do everything to catch up to make up for the lost time. Communication is everything--with your teammates, with your supervisor, with your client, etc..  Have designated resposnibilties and roles for every teammember so as to avoid all confusion and pointing of fingers.
6. In capstone I gained greater social skills more than anything, such as becoming better at negotiating, working with teammates, and preparing and presenting information. I also became highly developed in base engineering skills that come from being faced with problem and problem and having to adapt and solve such problems. 

## Dillon Williams
1. I believe we had a good overall team layout, each of us having sufficient prior knowledge to tackle the project. I think not having a team leader in the structure complicated the team. By that I mean there was confusion on who exactly needed to tackle what problem and a recluctance to take orders from others. Although the problems occured, the structure without a designated leader did help the team in the matter of treating all as equal.  
2. I believe the largest problem during the project was the ablility to receive all orders on time. We received around 3 out of 70 parts ordered in total. This could have caused major issues if the recevied parts had not been the required vital system pieces. It was also a small issue that some teammates would sometimes not want to do work most likely due to a fact that they were graduating soon. Although this occured, other teams experienced more of an issue that our team.  
3. If I knew there would have been such an issue receiving parts, I would have worked ahead far sooner so we could have gotten as much as possible. It also took time to figure out an exact layout for the signoffs. Once we noticed a pattern in the accpeted signoffs, the team quickly finished the reamining.  
4. Although we are in a team, it was best to designate **exactly** what each member would work on and **exactly** when it was expected to be finished. This way of communicating allowed the members to quickly finish sections of the project.  
5. Stay ahead on signoffs. There is date-based grading and delaying one grade can affect all of them. If you stay ahead then the grades will not be a concern.  
6. I improve majorly on my communication skills, with our team actually being voted best presentation. I also learned how to code GUI programs and how to develop communication betwwen a computer and PLC.  

## Ryan Reed 
1.  I think our organizational efforts paid off very well. If we were working on something (signoffs, experimentation, etc.), we were almost always doing it together. I think this helped all of us gain a better understanding of all subsystems and allowed us to help troubleshoot problems as a team. Something that I believe didn't go well was making sure parts were ordered. I understand that issues can arise, but I think we could have stayed more consistent and thorough with checking on ordering.
2.  The biggest unanticipated problem that occurred was not receiving our parts, namely the memory card for our PLC. Because of this we had to use the PLCs in the Prescott labs and had to use Studio 5000 (Allen Bradley) instead of TIA Portal (Siemens). Also because of this we had to find a new way to create an OPC client in Python.
3.  I would have been more thorough in my signoffs, especially the highest priority signoff. I would have also asked for help from my teammates sooner. With the knowledge that I have now on how signoffs should be done, I was definitely not thorough enough in the beginning and I would have tried to add as much detail and reasoning as possible.
4.  Documenting **everything**. When working on a project this large and for this amount of time, everything should be documented, backed-up, and organized. There were numerous times that having every documentation neatly organized helped us complete a task trivially.
5.  Listen to Professor Roberts' advice on staying ahead. Capstone can (and most likely will) get very crunched for time near the end of the semester. Front-loading would be beneficial in allowing you to complete experimentation and documentation at a reasonable time.
6.  I gained a deeper understanding of topics that I was already interested in, and some new understanding of topics that I was not familiar with thanks to doing signoffs. The technical presentation also helped deepen and solidify my knowledge on tools that I might have to use when I'm in the industry.

## Michel Turpeau
1. At first, I was worried due to my past experiences with teamwork. I will say, if consider myself the weakest link on the team that's a good sign. Organization was pretty easy since you can count on everyone to complete their work. On the technical side, everyone had background knowledge to help with the project. Even if there was any knowledge lacking, the team was always willing to do the research to find the solution the current problem.
2. The biggest problems stemmed from the ordering issues and my personal knowledge on safety. I originally forgot to dedicate a system to the safety of the machine and users. This meant I had to make a new subsystem without any prior knowledge on the subject or any of its components. After conducting the research and making the schematics, things became much clearer and the system was approved. As for the ordering, the issue was never exactly resolved with us instead focusing on what we did have and making the most of it.
3. I we were able to do it over again I would focus on two specifics things. First, it would have been useful to work on the detail designs over break. While it wasn't particularly expected of us, it would have helped a ton in the spring semester and greatly reduced the amount of stress we placed on ourselves. Second would have to be constantly checking in on our orders, making sure everything was handled properly. 
4. It is good for each person to be assigned their own tasked, but understand that we are a team. I anyone needs advice, they shouldn't be afraid to ask one of the team for help. Also, another best practice is to stay in contact with the team and alert them to any updates and changes to the project.
5. "15 minutes early, is being on time. Being on time is late." Always try to be ahead on your work. And even if we aren't expected to work on the weekend or during breaks, utilize this time to get ahead. While you miss out on some "fun times" it's better to get the work done and have free time afterwards, then it is to risk your project and work. Also, if you are working with another team in a different department, collaborate as much as possible. Every department has their own timeline and process, so don't assume they are on the same wavelength.
6. Thanks to capstone, I truly have a better understanding of what it means to be an engineer. I gained better skills for organization and collaborating with my teammates. I also learned plenty about using 3D modeling software like SolidWorks and AutoCAD, along with schematic software like KiCad. I also have done tons of writing and research, more than any other class before.

## Nidhay Patel
1. During the early days of Capstone 1, I was little concerned about how the project was going to get laid out for us as I believe our team had no idea whatsoever on how we were going to achieve this big goal, but I believe with every member having skills in different areas it helped our team a lot in achieving the target altogether. The team did face some technical problems with the first sign-off as I believe there were some discrepancies in what was expected and also with a bit of date-based grading but as a team I feel like we tackled the problem pretty good.
2. The biggest unanticipated problem that our team faced was of not getting the ordered parts. Although it didn’t really affect me as I was mostly in charge of software such as coding GUI, Database etc. But as a team we would have loved if we had parts arrive on time as our team was really enthusiastic and was looking forward to have the project completely built and functionally running by the end of the Capstone course.
3. One thing I would’ve done differently is to start early on the sign-offs. Our team had some major problems with not having sign-off done on when we have expected to as a result it ended up affecting our ordering grade. Our team had already decided on what each person would be working on at the end of Capstone I but still nobody was prepared at the start on next course, but I’m happy that even though it didn’t happen how we would have expected it to but it’s the fact that the team came together and countered every problem and put their best efforts to get everything done on time.
4. There were times where the team didn’t really know what plan to go with and at that time understanding different peoples thought and considering them with the idea of where they’re coming from helped the team with different possibilities. More people mean more brain power. Also, knowing what each individual was supposed to do really helped the team and have clear vision to when the team would be done with some of the things.
5. Start early no matter how little of a task it is. It is easy to get behind in the course given the bigger picture. It’s easy to get caught up with deadlines, to-do lists, finishing things on time for other classes, but at the same time do take the time to consider both successes and failures so that the team may not only reinforce what works but also concentrate on what might be done better the next time.
6. There’s a lot of things that I learned through capstone. Firstly, working with different people meaning different mindset. The team sometimes would have opposing ideas but working out together as a team is something that I’ve added to my skillset. Another thing would be communication. It is easy to give casual presentation but when it comes to presenting something technical it takes a lot more efforts in researching and getting to the core of it so that you understand how, and why something works the way it does. This really helped me with my individual sign-offs and also gave me an insider on what it might look like on an industry level.

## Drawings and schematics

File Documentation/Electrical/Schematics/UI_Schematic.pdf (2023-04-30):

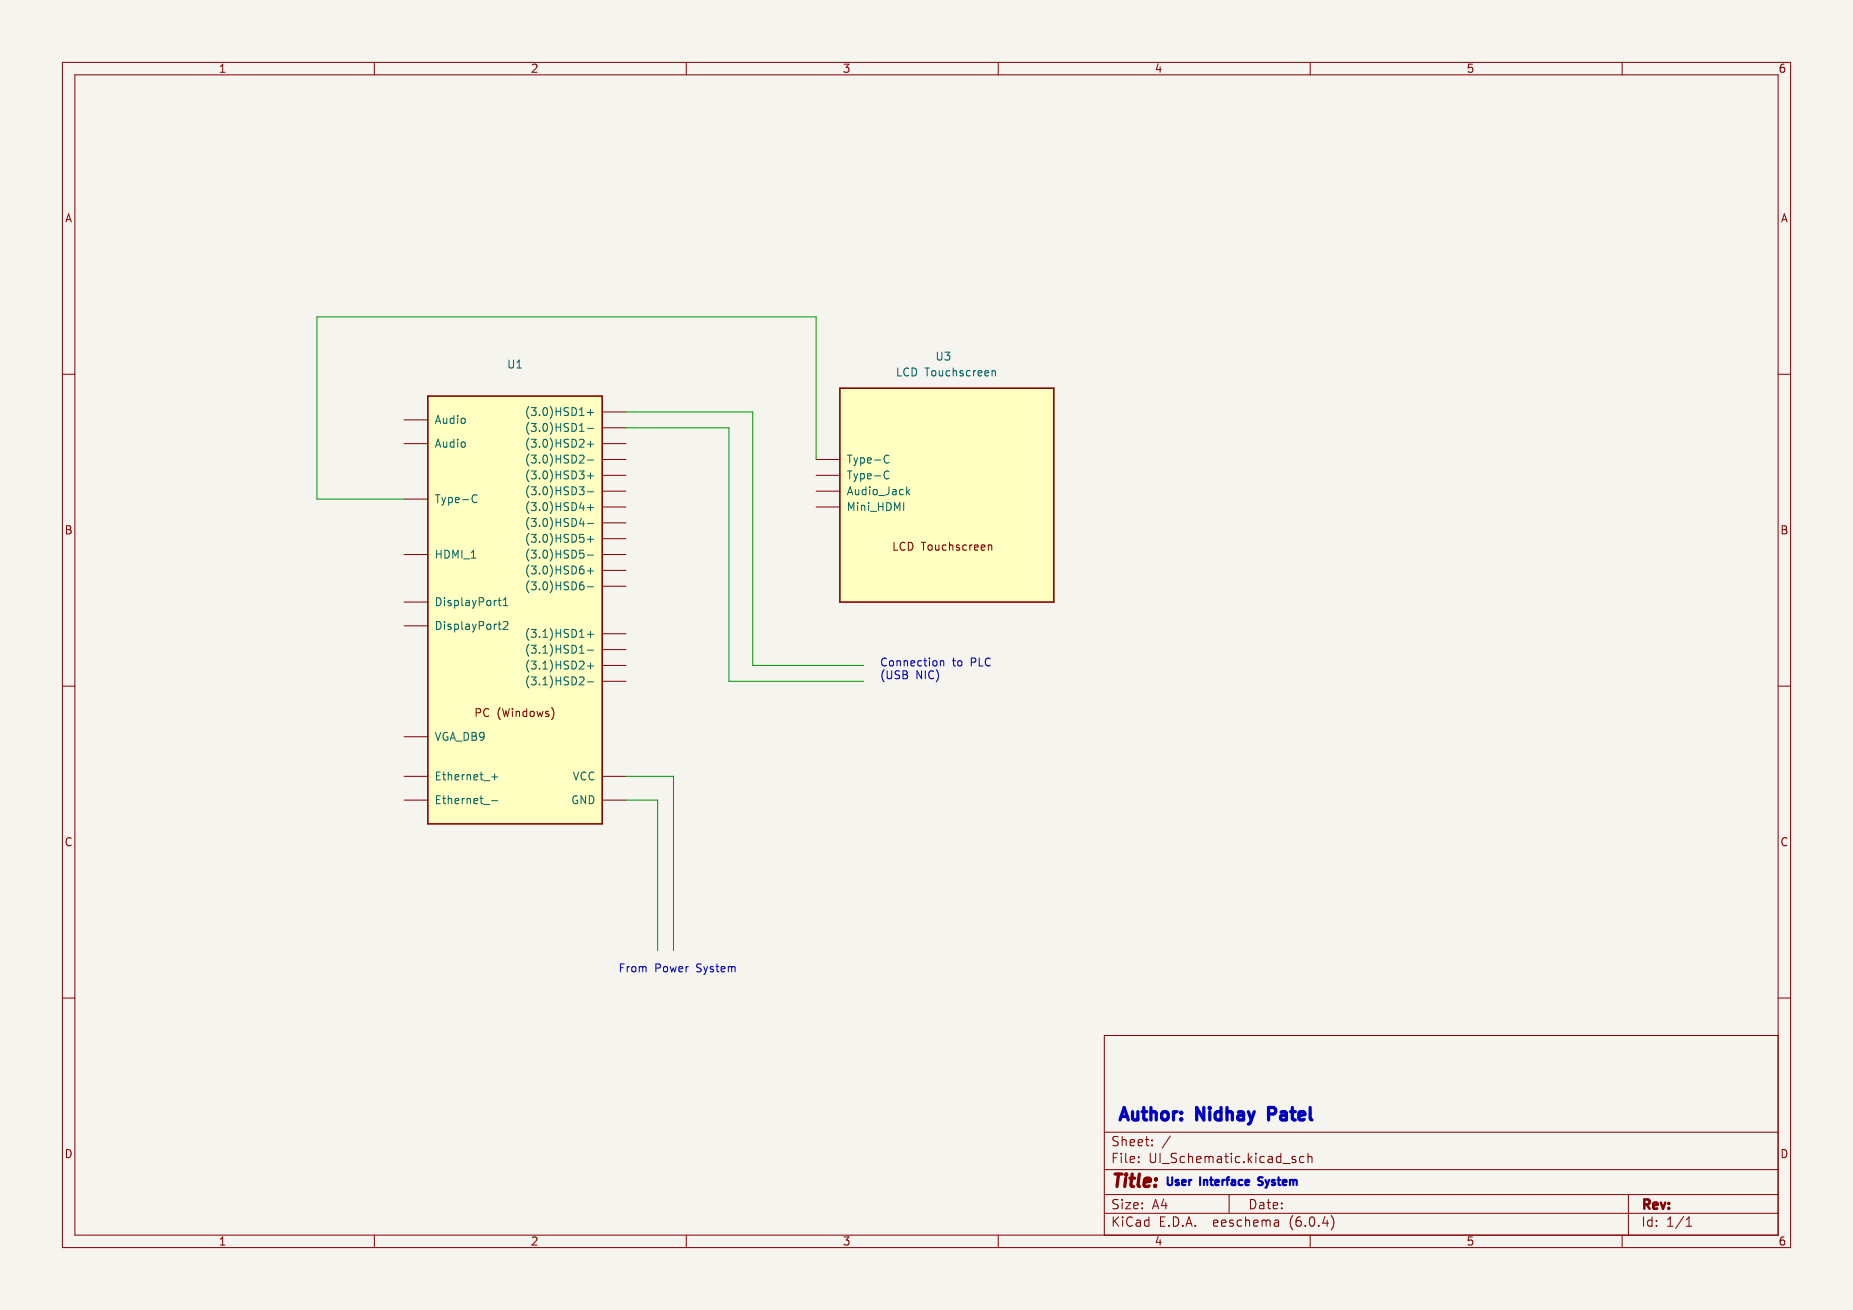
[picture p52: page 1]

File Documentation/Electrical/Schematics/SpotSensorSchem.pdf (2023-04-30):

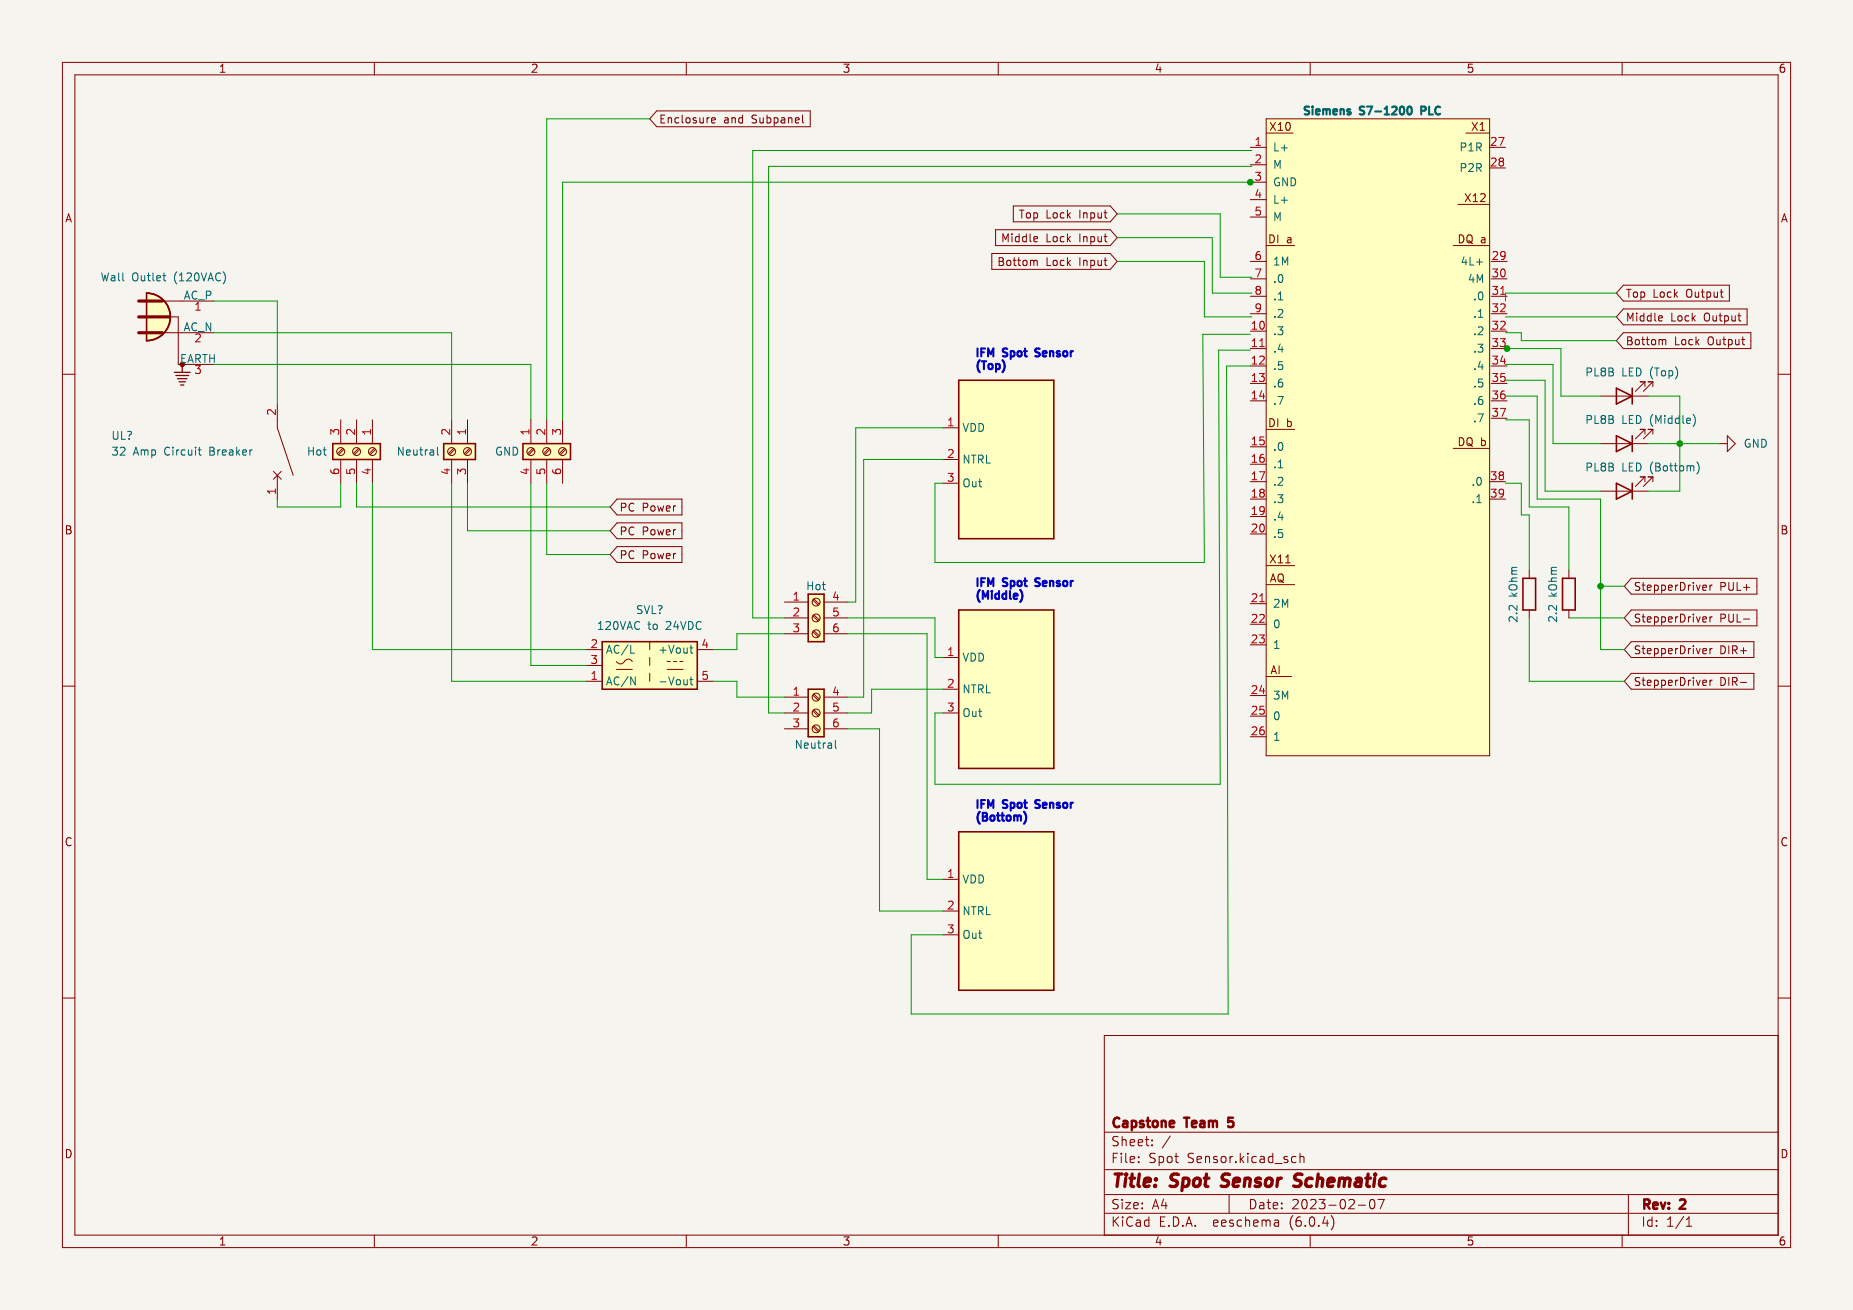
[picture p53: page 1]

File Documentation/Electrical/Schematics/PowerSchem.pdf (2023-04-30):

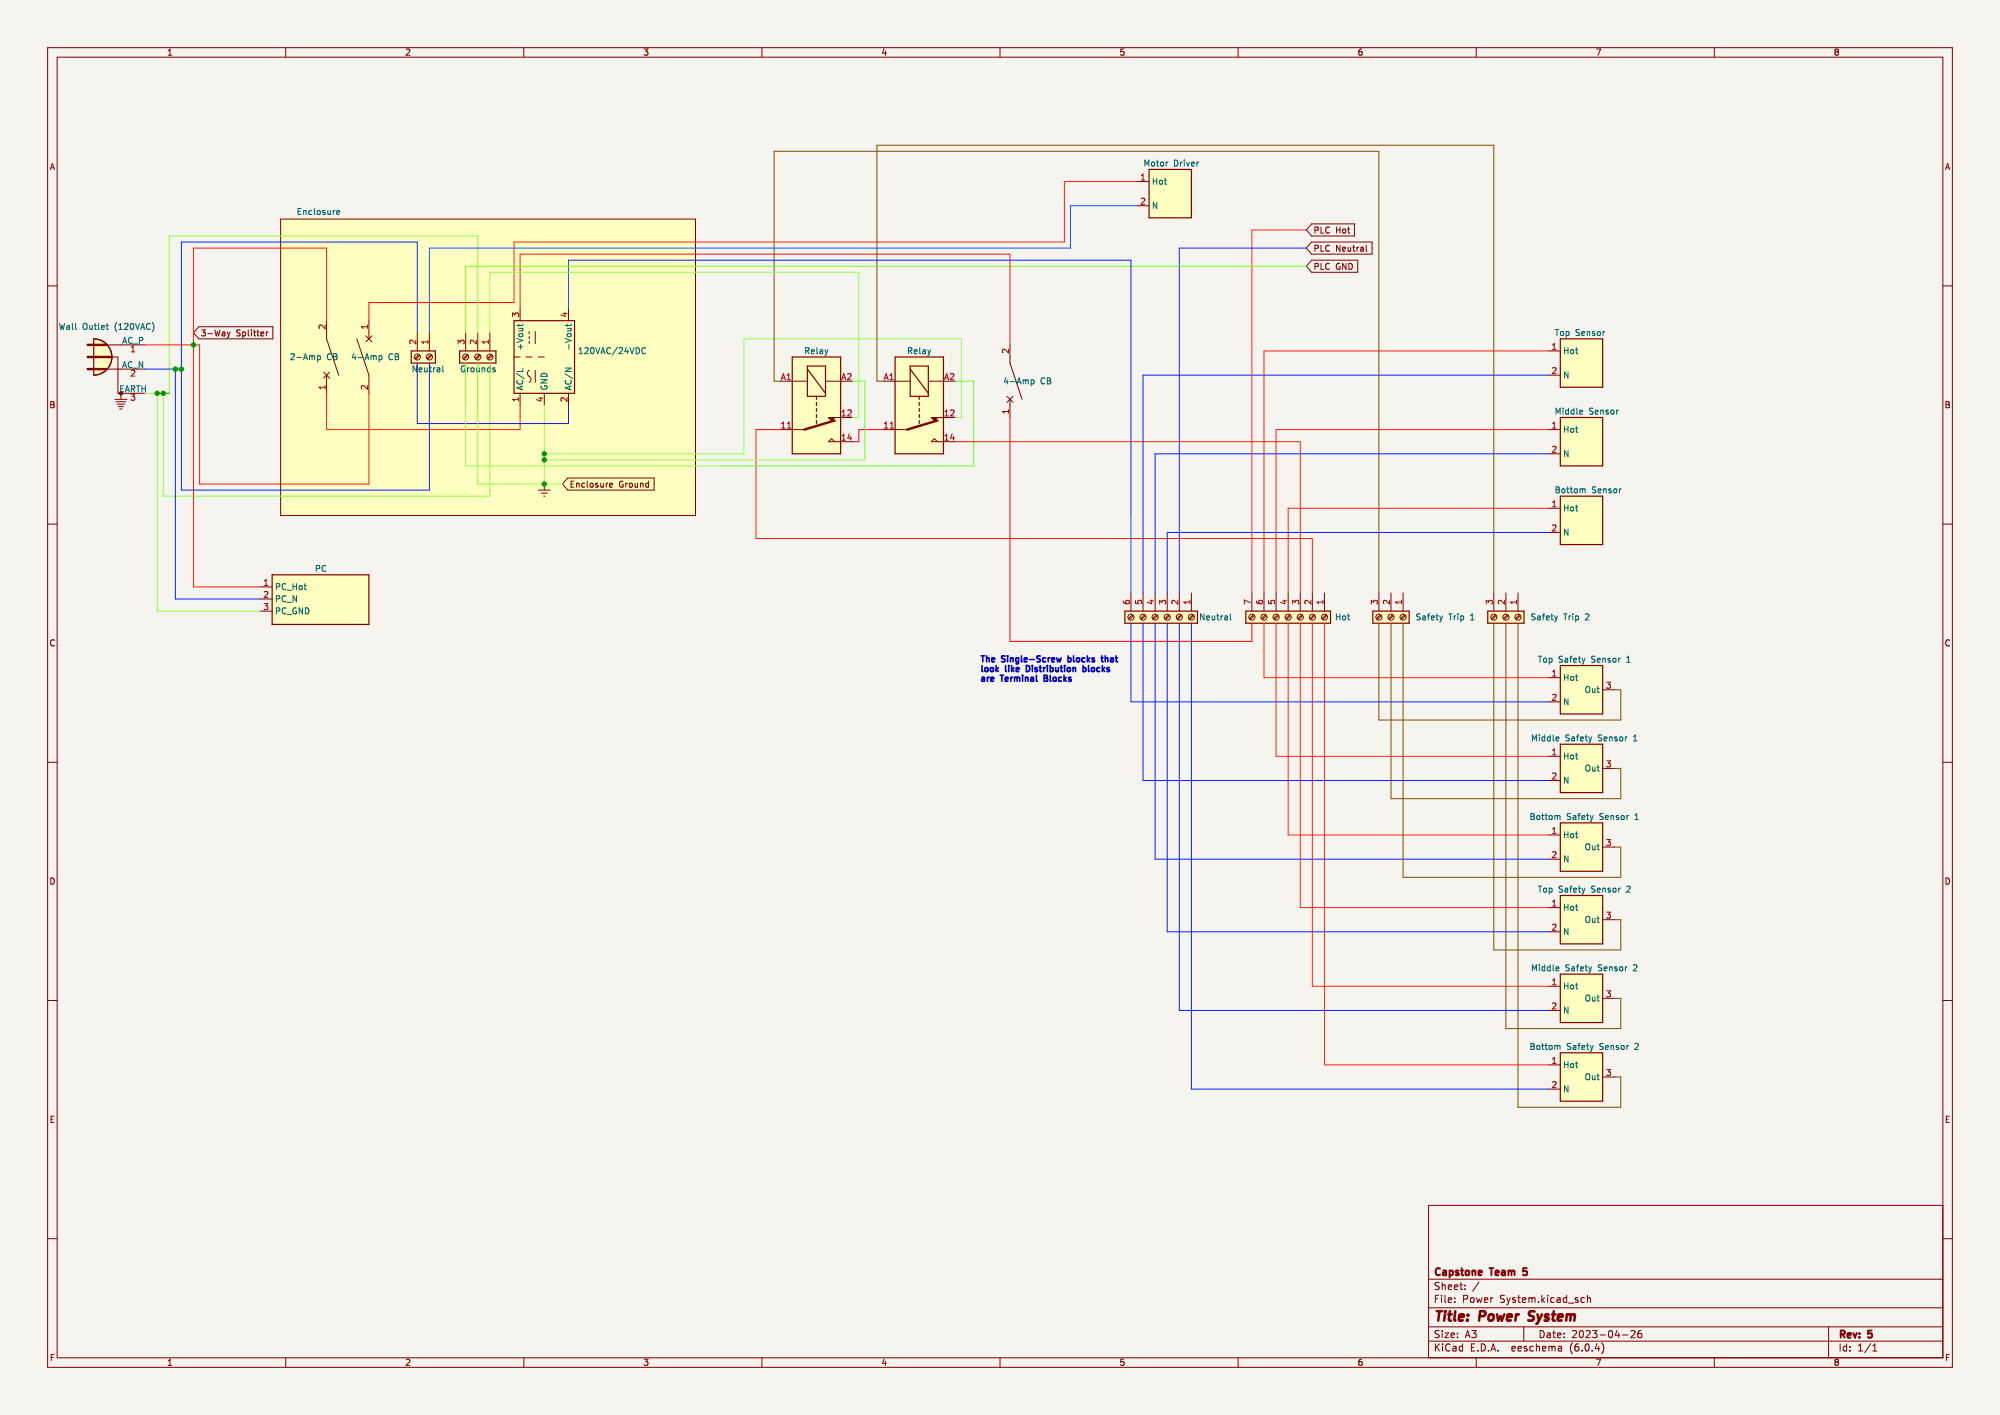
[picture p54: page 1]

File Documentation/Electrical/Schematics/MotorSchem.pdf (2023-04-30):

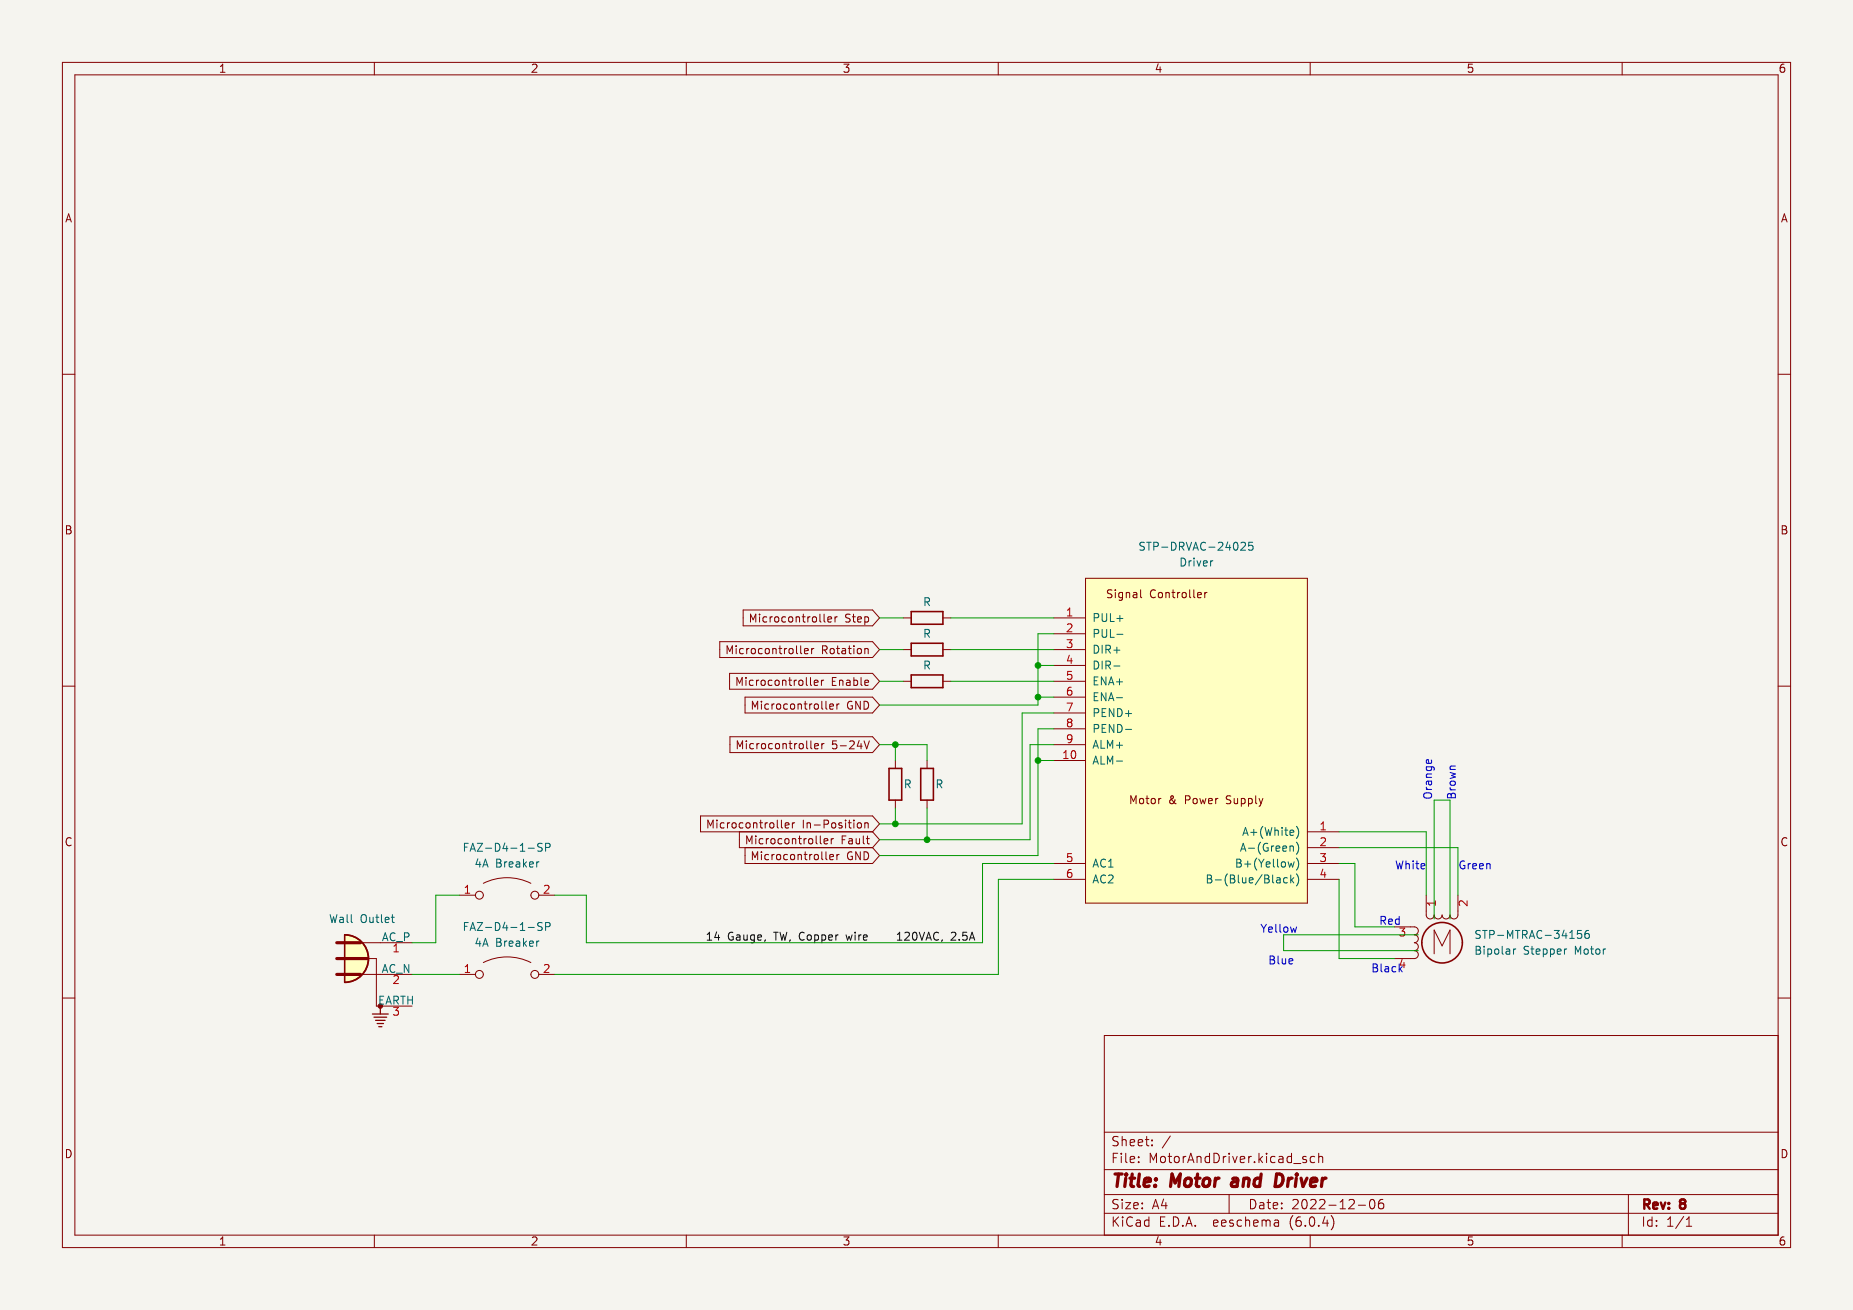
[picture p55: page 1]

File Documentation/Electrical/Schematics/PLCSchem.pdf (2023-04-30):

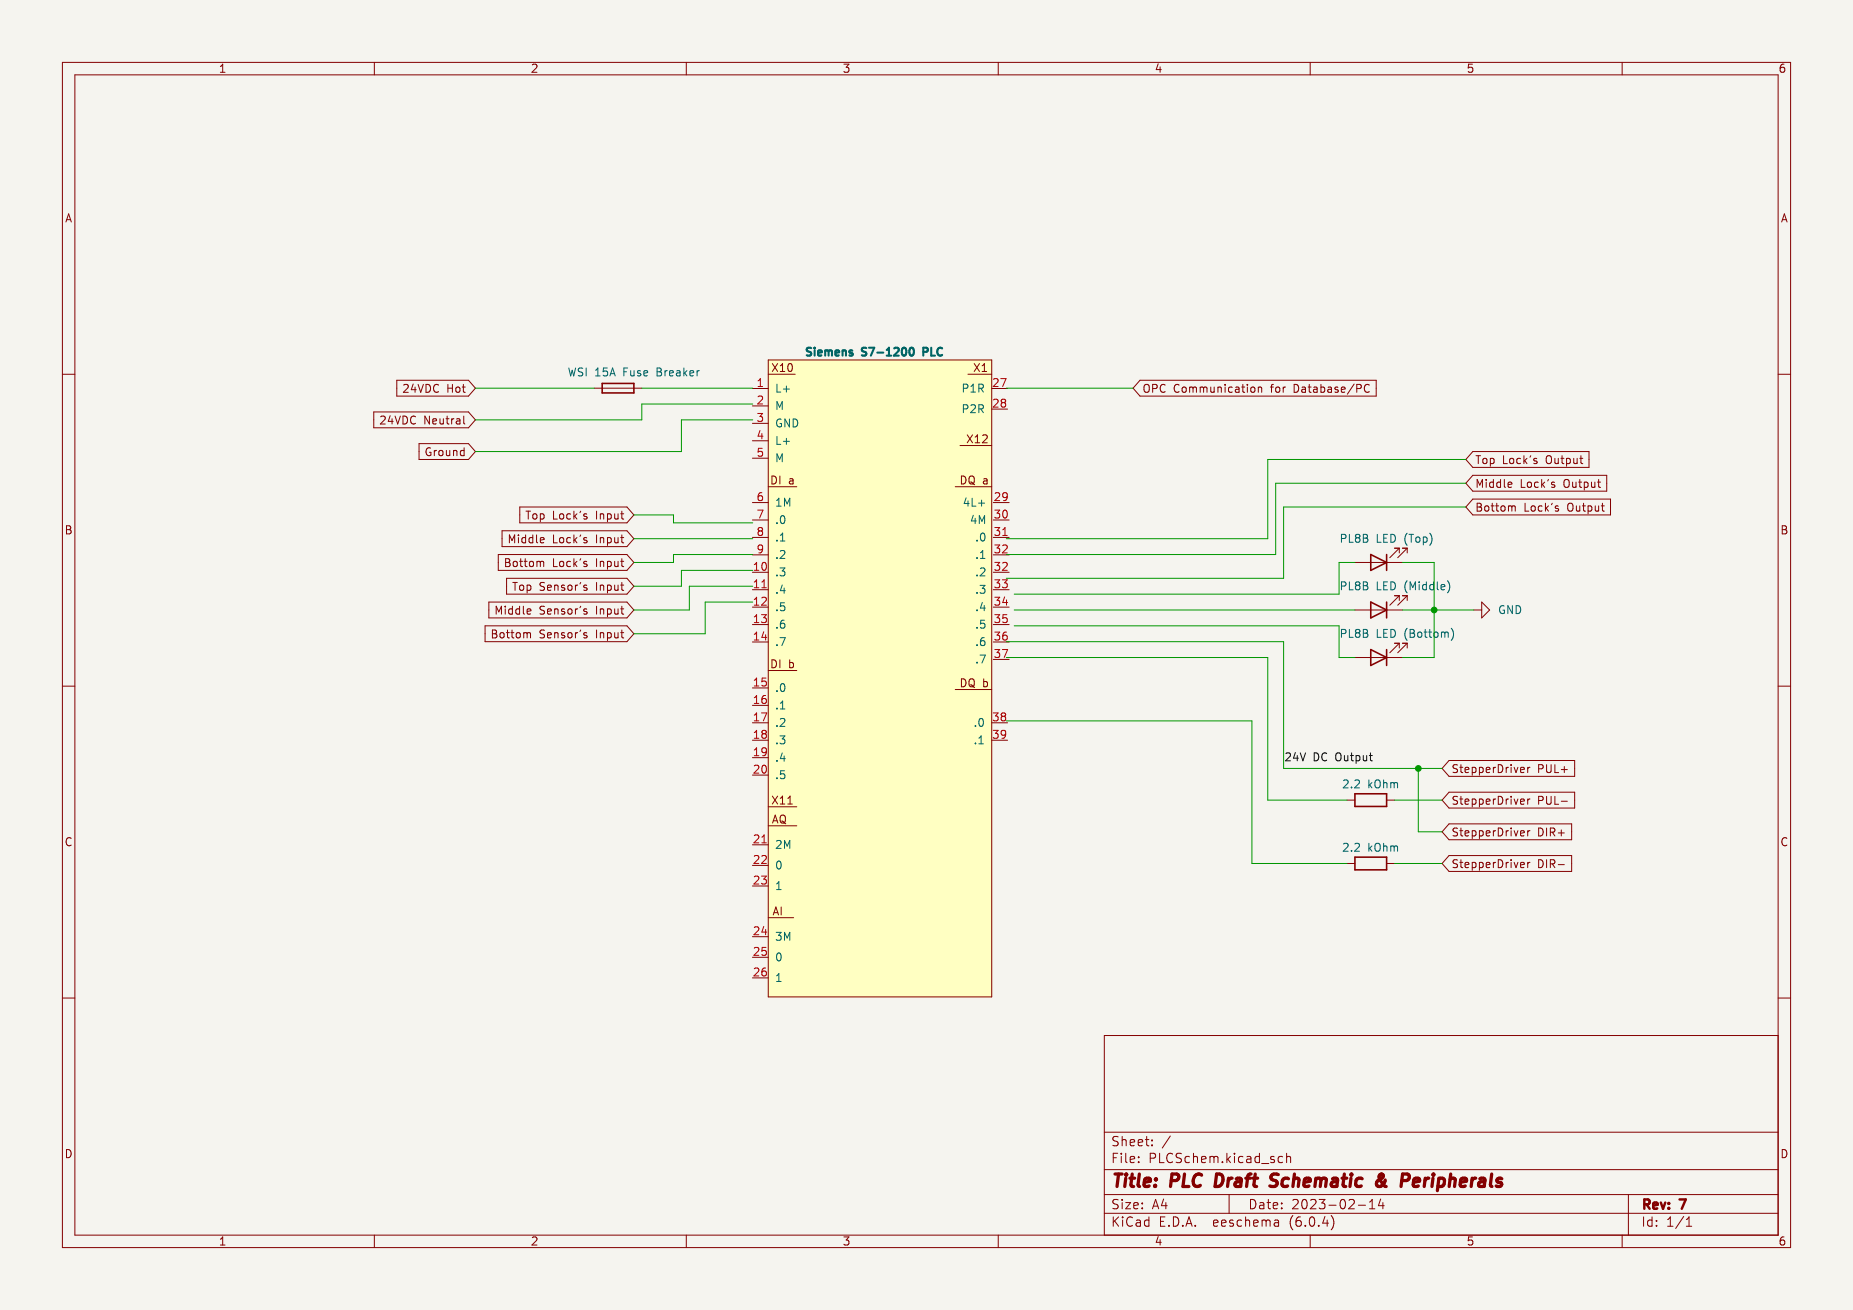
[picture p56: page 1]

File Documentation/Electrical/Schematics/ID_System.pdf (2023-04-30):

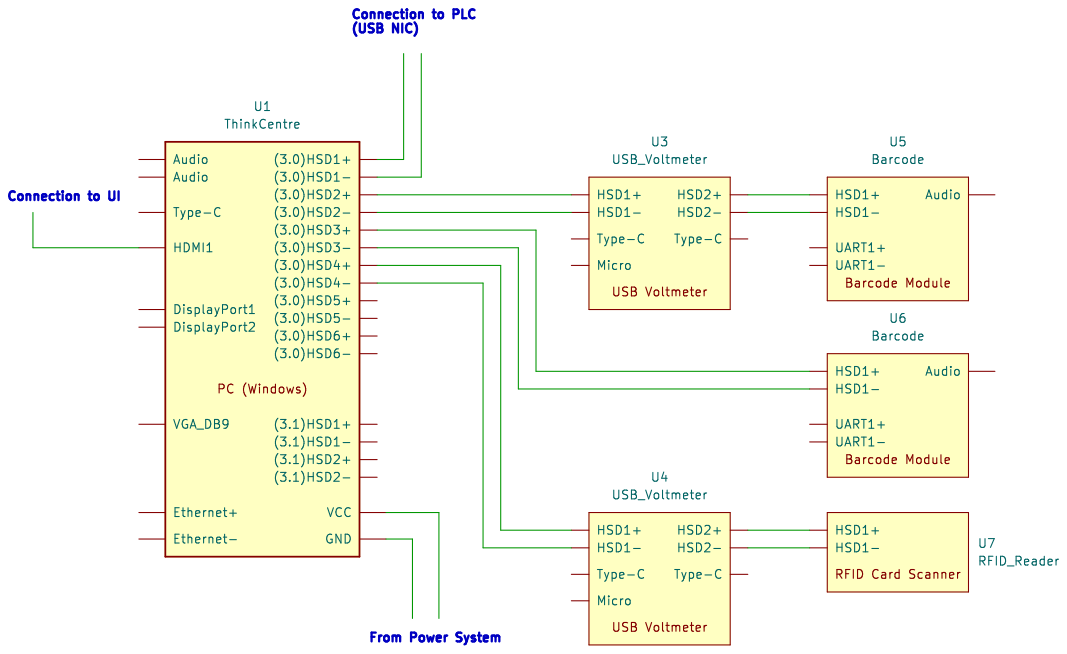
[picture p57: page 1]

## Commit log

2022-11-08 Create Team5-signoff-Motor
2022-11-10 Create Motor System.md
2022-11-10 Update Motor System.md
2022-11-10 Requesting signoff for Motor System
2022-12-01 Team5 customization (#8)
    * Delete Budget.xlsx
    * Delete Conceptual Design.pptx
    * Delete Conceptual_Design_Draft.docx
    * Delete Conceptual_Design_Revision.docx
    * Delete Proposal_Revisions_Final.docx
    * Delete Team5_project_Proposal_Final.pptx
    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
    [Budget.xlsx]
2022-12-07 Update Sensors.md
    Edited Grammar and sentence structure.
2023-01-31 Update Security_Locks.md
    Minor edits, still working on 2d and 3d schematics.
2023-02-02 Create Power System.md
2023-02-02 Update Power System.md
2023-02-08 Update Security_Locks.md
    Updated 3D model.
    Re-added Inductance Sensors.
    -Adjusted BOM
    Slightly adjusted constraints.
    Constraints still need work.
2023-04-30 Add files via upload
    Hi dillon
    [1798A21_Surface-Mount_Hinge_with_Holes.SLDPRT, 47065T241_Silver Corner Bracket.SLDPRT, 47065T279_T-Slotted Framing.SLDPRT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]
